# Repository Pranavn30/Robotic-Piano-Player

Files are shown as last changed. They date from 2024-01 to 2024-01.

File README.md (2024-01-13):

# Robotic-Piano-Player

Youtube Demonstration:

Robotic Piano Player (https://youtu.be/aeWdHynBX10)

The motivation of the project was to be able to emulate the functionality of a human playing the piano, mimicking the two "hands" of a human as well. We created this two hand structure by having two modules that move independently on two different belt drive linear actuators. The right hand plays three octaves and the left hand plays two octaves. Each hand is composed of 12 DC doorlock actuators which act as the fingers, and which are turned on and off by using I2C signals from GPIO expanders. These hands are then housed on custom 3D printed structures to hold all of the actuators in an exact and precise manner over the keys. Finally, the project has an LCD functionality which plays the music, as well as stops in and returns the hands to "home" position. The music files are downloaded and processed in a custom python script which decodes them, and is sent over USB to UART to the STM32. The data is then preprocessed within the firmware, optimizing the hand positions by grouping notes together, looking for movement opportunities, and overall making the system as efficient as possible. There is also speaker functionality (see below for further description).

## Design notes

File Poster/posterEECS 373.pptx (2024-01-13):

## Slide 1

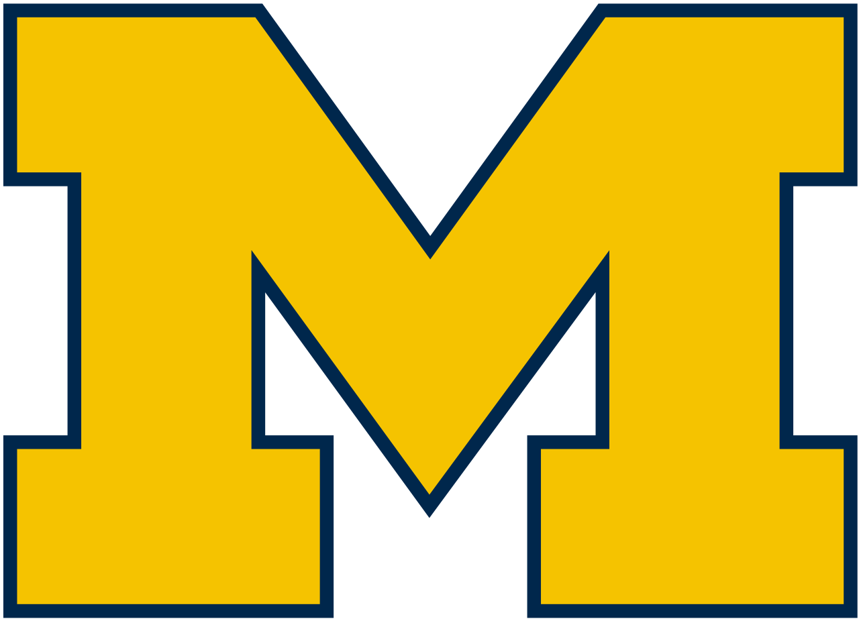
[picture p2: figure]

Robotic Piano Player

Pranav Narayanan, Daniel Moon, Zo-Vic Shong, Jesus Vidal Sanchez
{pranavn, danymoon, zovic, jesusvs}@umich.edu

EECS 373

MUSIC AND TECHNOLOGY COME TOGETHER TO EMULATE HUMAN PERFORMANCE SKILLS

- LCD screen allows the user to select which song will be played by the system.
- Uses a graphic library to display the interface
- Features a touchscreen so that the user can interact with the system
- Communicates with the STM through SPI

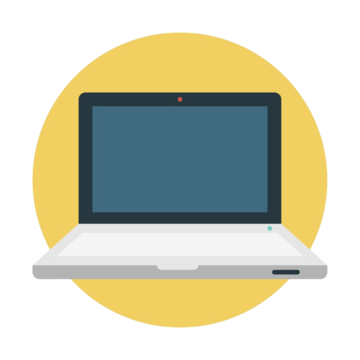
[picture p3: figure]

UART

It's Beginning To Look A Lot Like Christmas….

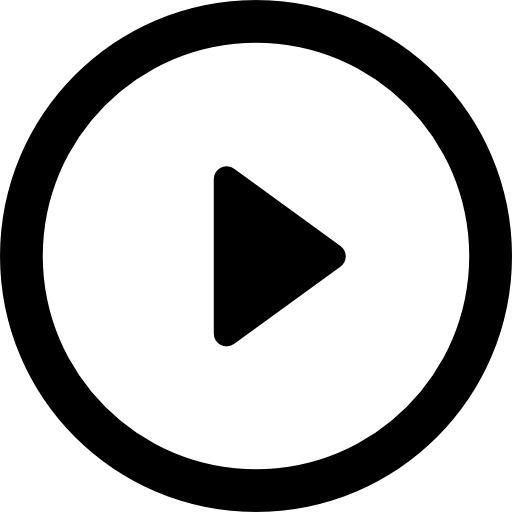
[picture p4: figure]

SPI

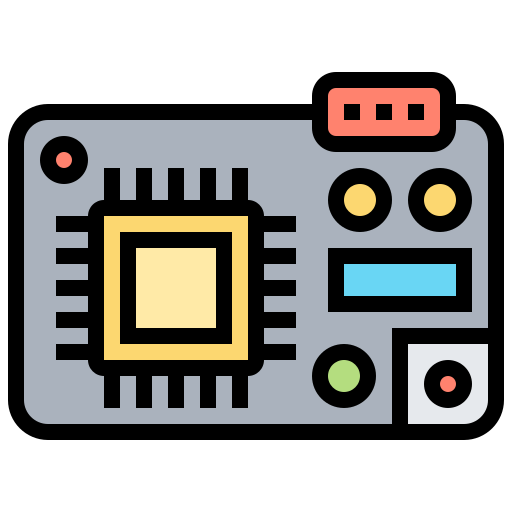
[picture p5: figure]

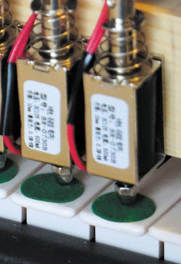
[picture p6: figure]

two hands
(3D printed structure)

Linear Actuators

Electromechanical
Belt Linear Actuator

- MIDI information is split into the respective two hands and proceeds through a complex algorithm to find the optimum times to move, and the ideal positions to play notes
- Entire system is controlled by timer interrupts which manage priorities and ordering of note playing

Arm Cortex M3

- The PC decodes information from locally stored MIDI files using Python

Python Script

- The Electromechanical Belt is used to move the hands horizontally in order to reach different note registers.
- We are using two belts, one for each hand so that they can move independently from each other. Each belt is moved by a Stepper Motor, connected to a Stepper Controller that makes them run at 2.8A of current.
- They are powered by a power source.

DAC

Speaker

- DC actuators are used to emulate human fingers:
- 12 dc actuators attached to each one of the two hands allow for triggering notes individually.
- The STM controls the voltage needed to trigger each actuator
- GPIO expanders needed to be used. They connect the actuators to the STM and use I2C protocol for communication.

- Due to the fact that some notes cannot be reached by our design, we implemented an external speaker.
- We will play notes out of range through the speaker instead of hitting keys
- It generates a sine wave to the corresponding frequency of the note intended to be played. The input to the speaker is the STM´s DAC.

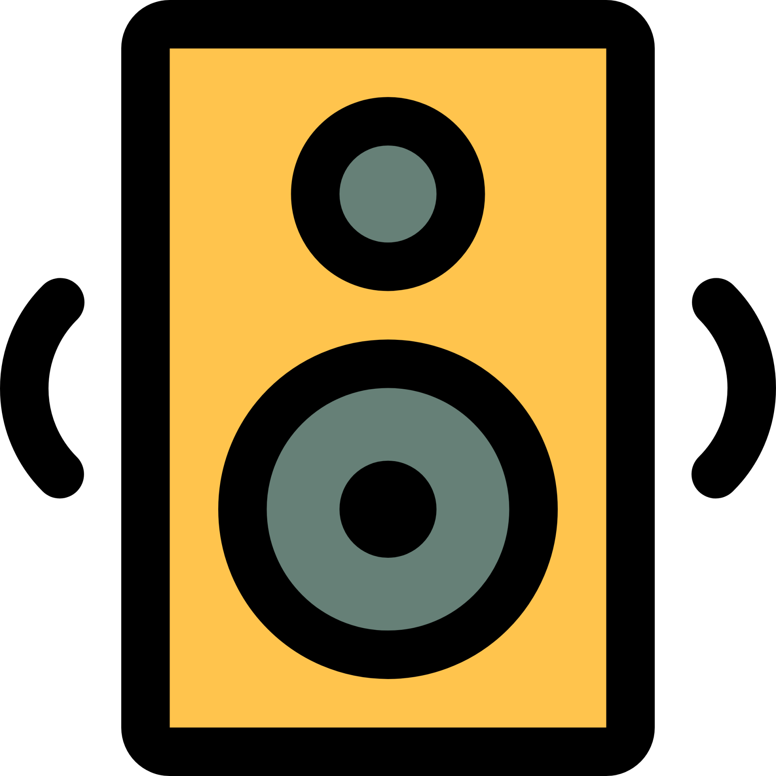
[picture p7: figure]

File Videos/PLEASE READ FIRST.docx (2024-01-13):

Hello Professors Sample and Smith, the best version of the video is linked in this document and in the README file within the digital archive folder, which includes a detailed description of the various parts. The video in here is the same but lacks the description

Link (https://youtu.be/aeWdHynBX10)

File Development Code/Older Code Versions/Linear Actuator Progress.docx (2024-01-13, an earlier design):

Linear Actuator Specifications:

2023.11.07

- Wire MCU, stepper motor controller, and stepper motor
- First attempts at coding, unsuccessful

2023.11.09

- Decide on belt drive for movement
- Successfully move stepper motor for first time

2023.11.11

- Use PWM for step control
- Get it moving faster
- Maximum step interval seems to depend on maximum voltage

2023.11.13

- Look up table (notes to distances)
- Equations for activation time to distance

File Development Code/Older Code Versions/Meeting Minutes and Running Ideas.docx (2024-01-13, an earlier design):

Interrupts get used if it is live actuation of the door lock actuators

FPGA lidar

Predictive algorithm using interrupts to determine next optimal position

Serial input in 2 note packets, preprocessed, determine optimal position of hand to enhance speed - possibly do this using fpga

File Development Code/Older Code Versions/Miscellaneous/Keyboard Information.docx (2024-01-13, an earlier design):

Full Keyboard Span - 33.5 Inches, 85 cm

White Key Thickness (also distance between white keys) - ⅞ Inches, 2.2 cm

Black Key Thickness - ⅜ Inches, 1 cm

Black Key Distance (#F, #G, #A) - 1 1/16 inches, 2.7 cm

Black Key Distance (#C, #D) - 1 ⅛ inches, 2.8 cm

Black Key Distance (#A, #C; #D, #F) - 1 ⅝ Inches, 4.2 cm

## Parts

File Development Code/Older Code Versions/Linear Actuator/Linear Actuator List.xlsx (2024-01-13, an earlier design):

Name | Length (inches) | Price | Link
Belt Drive Motorized Linear Stage Actuator 600MM | 23.622 | $209 | https://www.amazon.com/Motorized-Linear-Actuator-Motion-Position/dp/B07V1LRFPT
High Speed 700 MM 28 INCH Stroke Belt Drive | 28 | $195 | https://www.amazon.com/Stroke-Linear-Motion-Actuator-Position/dp/B07STNGVWS?sp_csd=d2lkZ2V0TmFtZT1zcF9hdGY
FUYU FSL40 Linear Guide Table | 19.685 | $195 | https://www.amazon.com/FUYU-Linear-Actuator-Motorized-Stepper/dp/B077Q8LVLW
RATTMMOTOR ZBX80 600mm | 23.622 | $215 | https://www.amazon.com/RATTMMOTOR-Actuator-Aluminum-Sliding-Ballscrew/dp/B09MYK424S
NEMA 23 Stepper Motor |  |  | STEPPERONLINE 3PCS Nema 23 CNC Stepper Motor 2.8A 1.26Nm/178.4oz.in 56mm Bipolar for Hobby CNC Kit - Amazon.com (https://www.amazon.com/STEPPERONLINE-Stepper-Motor-179oz-Bipolar/dp/B00QG1ZF48)

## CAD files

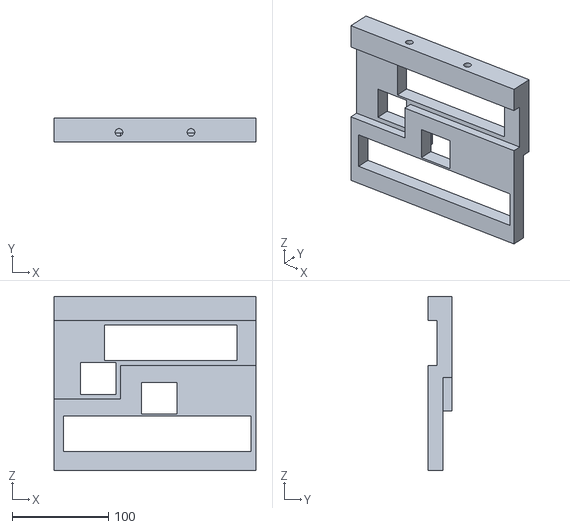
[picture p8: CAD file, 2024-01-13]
3D Print Files/DC Actuator Holder.STL
210.4 x 25.0 x 181.5

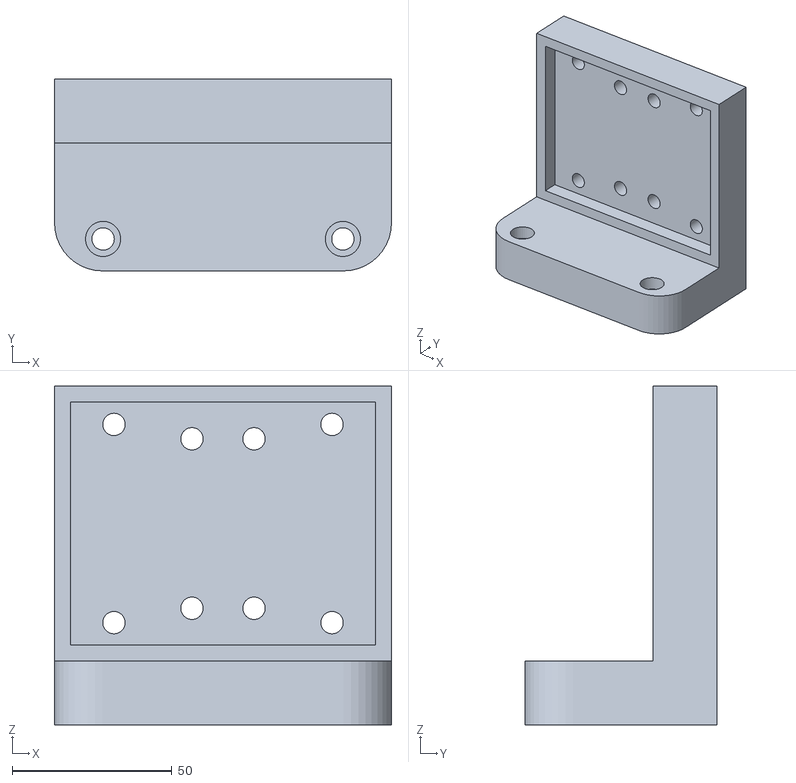
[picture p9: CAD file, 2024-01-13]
3D Print Files/DC Actuator Carriage Connector.STL
105.4 x 60.0 x 106.0

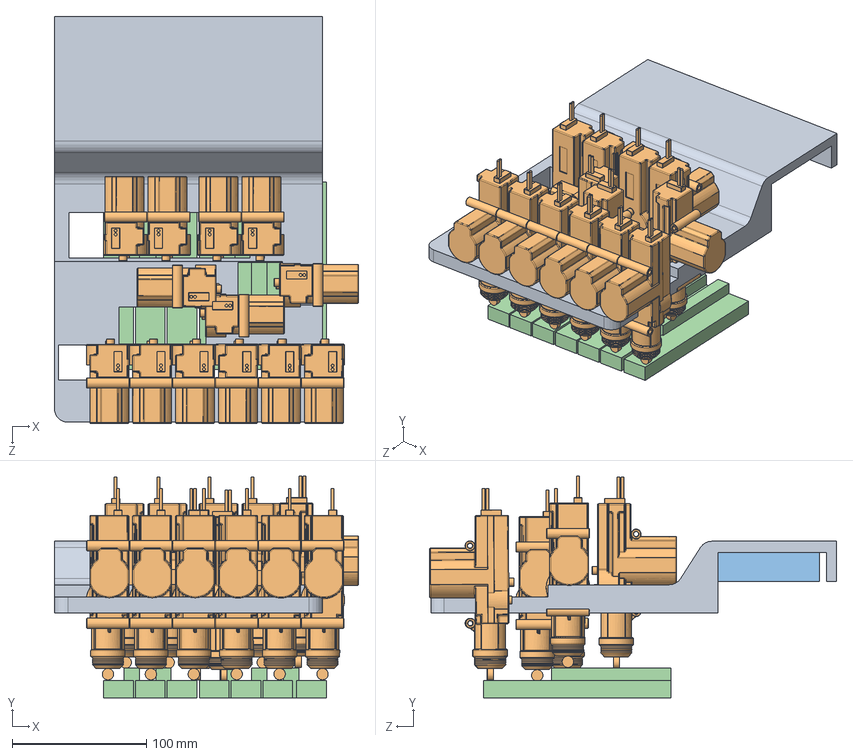
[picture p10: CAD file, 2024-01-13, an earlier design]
Development Code/Older Code Versions/CAD/373_Piano_Robot_Assembly_V2.SLDASM
226.8 x 165.2 x 303.5 mm
Piano_Keys
Rail_Carriage
DC_Actuator x 13
Linear_Actuator_Holder

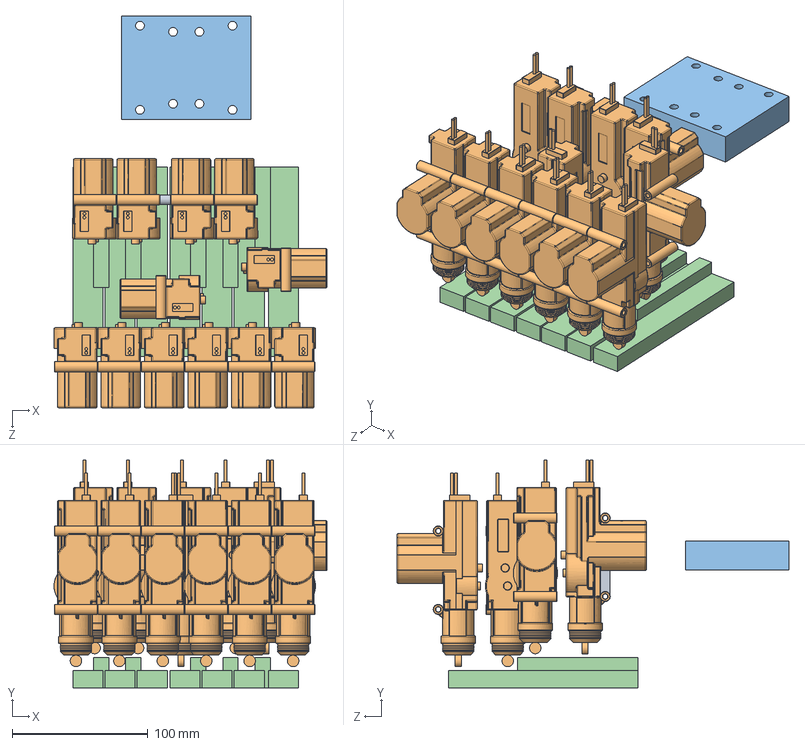
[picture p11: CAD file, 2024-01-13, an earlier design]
Development Code/Older Code Versions/CAD/373_Piano_Robot_Assembly.SLDASM
201.1 x 167.6 x 288.5 mm
Piano_Keys
Rail_Carriage_With Holes
DC_Actuator x 12
DC_Actuator_Black_Key_Spacer

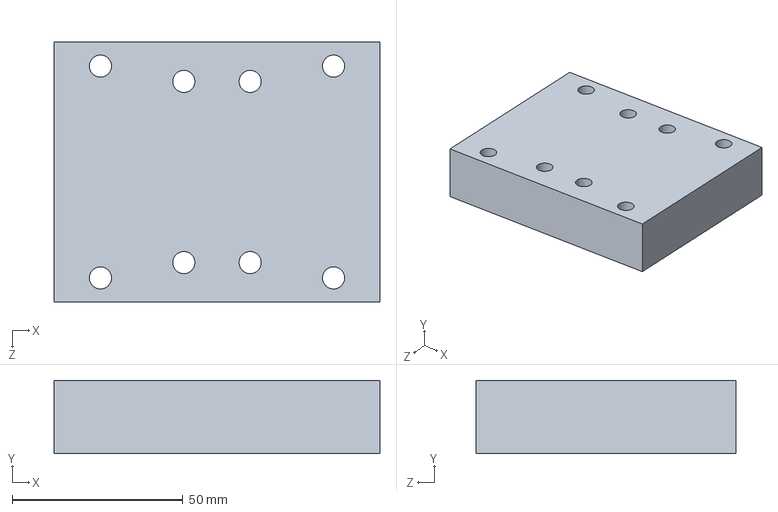
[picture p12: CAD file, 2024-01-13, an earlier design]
Development Code/Older Code Versions/CAD/Rail_Carriage_With Holes.SLDPRT
95.4 x 21.5 x 76.0 mm

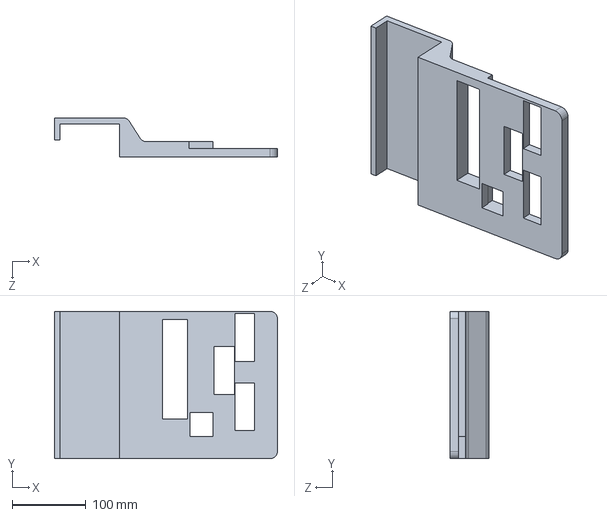
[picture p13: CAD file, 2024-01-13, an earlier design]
Development Code/Older Code Versions/CAD/Linear_Actuator_Holder.SLDPRT
302.5 x 200.0 x 53.5 mm

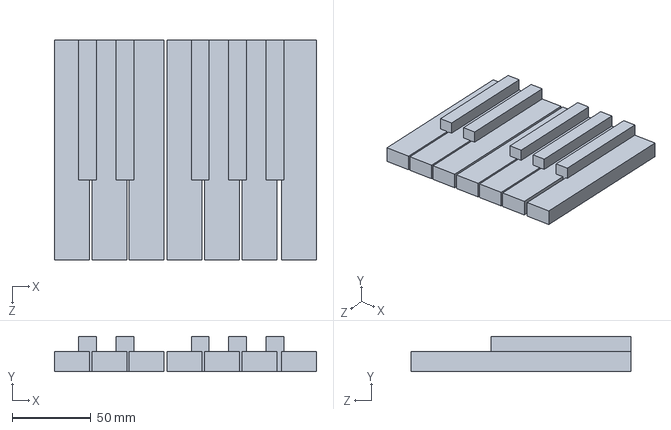
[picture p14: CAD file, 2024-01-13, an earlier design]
Development Code/Older Code Versions/CAD/Piano_Keys.SLDPRT
166.3 x 22.2 x 139.7 mm

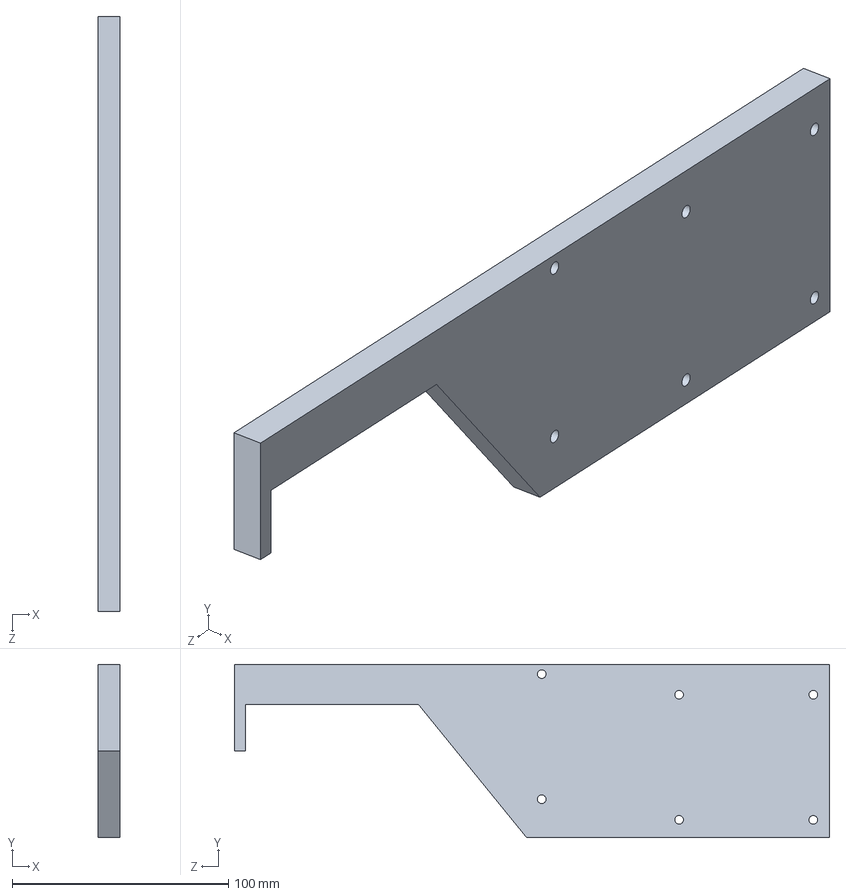
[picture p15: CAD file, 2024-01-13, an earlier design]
Development Code/Older Code Versions/CAD/Linear_Actuator_Support_Plate.SLDPRT
10.0 x 80.0 x 275.0 mm

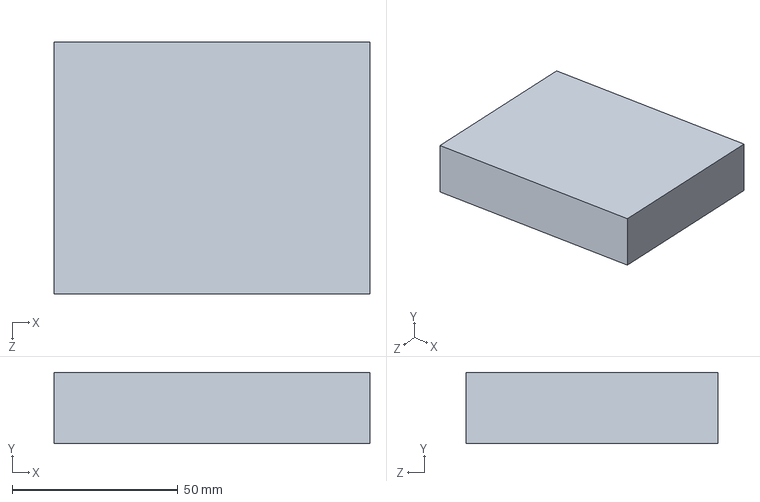
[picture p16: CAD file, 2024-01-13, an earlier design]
Development Code/Older Code Versions/CAD/Rail_Carriage.SLDPRT
95.4 x 21.5 x 76.0 mm

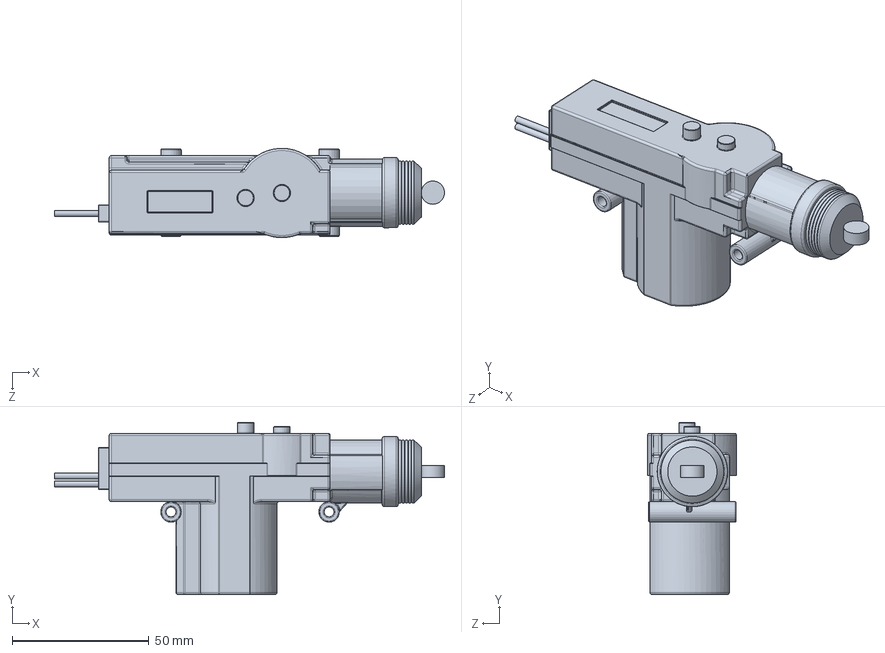
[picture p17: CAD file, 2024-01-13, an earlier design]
Development Code/Older Code Versions/CAD/DC_Actuator.SLDPRT
142.6 x 63.0 x 32.6 mm

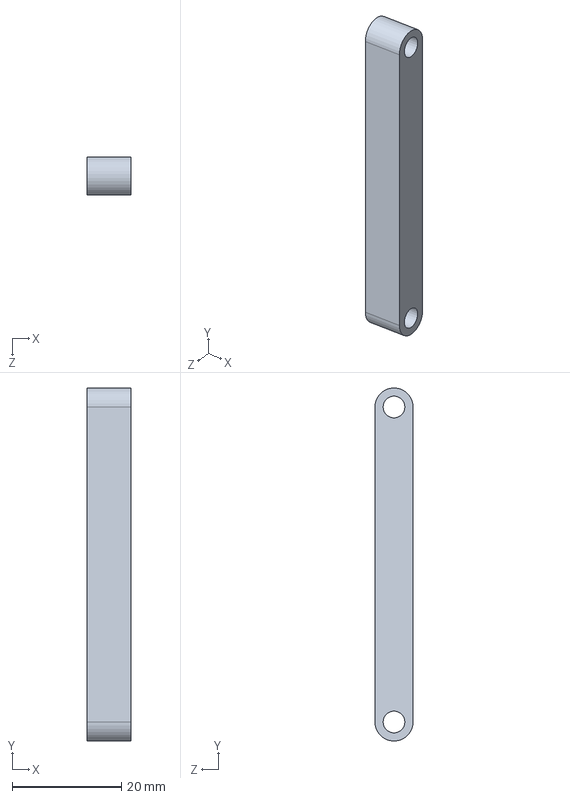
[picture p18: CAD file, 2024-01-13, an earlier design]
Development Code/Older Code Versions/CAD/DC_Actuator_Black_Key_Spacer.SLDPRT
8.00 x 64.8 x 7.00 mm

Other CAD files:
Development Code/Older Code Versions/CAD/DC_Actuator_Carriage_Connector_[PRINT].SLDPRT
Development Code/Older Code Versions/CAD/DC_Actuator_Holder_[PRINT].SLDPRT

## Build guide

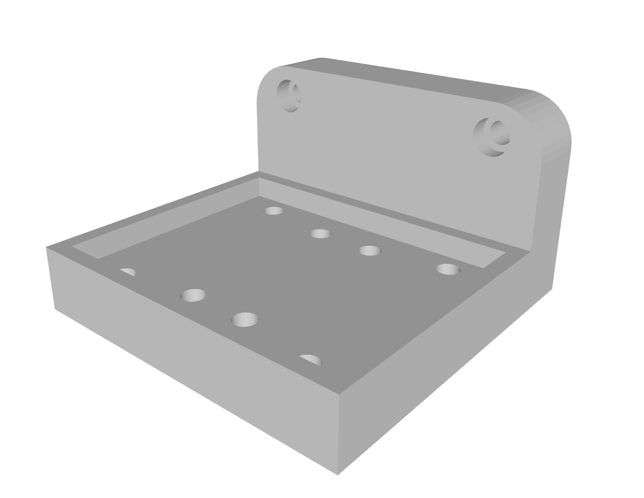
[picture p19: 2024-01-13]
3D Print Files/DC Actuator Carriage Connector.png

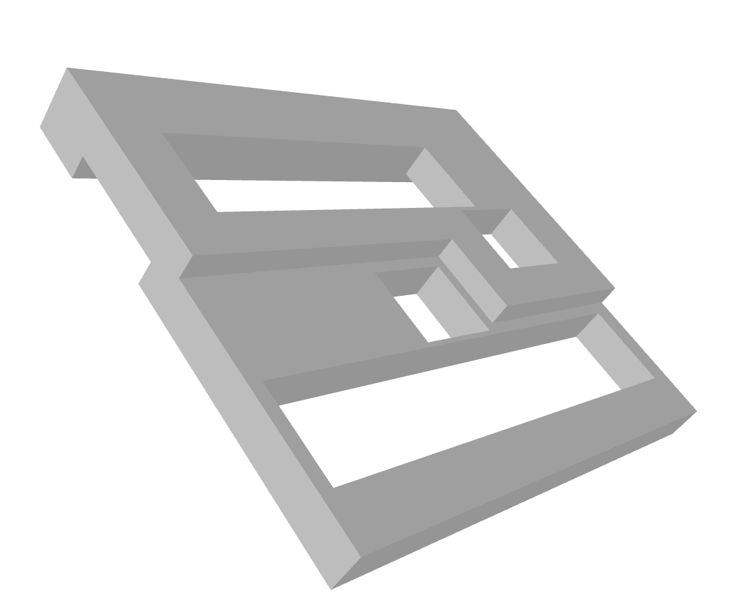
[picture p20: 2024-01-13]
3D Print Files/DC Actuator Holder.png

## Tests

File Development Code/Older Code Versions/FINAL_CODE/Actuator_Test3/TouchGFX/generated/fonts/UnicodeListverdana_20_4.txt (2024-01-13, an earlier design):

32
48
49
50
51
52
53
54
55
56
57
63
65
66
67
68
69
70
71
72
73
74
75
76
77
78
79
80
81
82
83
84
85
86
87
88
89
90
95
97
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

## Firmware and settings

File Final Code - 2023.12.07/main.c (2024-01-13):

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
/* Includes ------------------------------------------------------------------*/
#include "main.h"
#include "app_touchgfx.h"

/* USER CODE BEGIN Includes */
#include "math.h"
#include "stdlib.h"

/* USER CODE END Includes */

/* USER CODE BEGIN PD */
#define maxLetters 50

#define TIM7_PRSC 12
//look up table for sin wave generation
#define LUT_SIZE 100
uint16_t SIN_LUT[LUT_SIZE];
const double AMP_PCENT = 90.0; //amplitude of sine wave (0- 100)

/* USER CODE END PD */

CRC_HandleTypeDef hcrc;

DAC_HandleTypeDef hdac1;

I2C_HandleTypeDef hi2c1;
I2C_HandleTypeDef hi2c2;
I2C_HandleTypeDef hi2c3;
I2C_HandleTypeDef hi2c4;

SPI_HandleTypeDef hspi1;
SPI_HandleTypeDef hspi2;
DMA_HandleTypeDef hdma_spi1_tx;
DMA_HandleTypeDef hdma_spi2_tx;

TIM_HandleTypeDef htim2;
TIM_HandleTypeDef htim3;
TIM_HandleTypeDef htim4;
TIM_HandleTypeDef htim5;
TIM_HandleTypeDef htim7;

UART_HandleTypeDef huart2;
UART_HandleTypeDef huart3;

/* USER CODE BEGIN PV */
uint8_t RX_Buffer[5]; //"Interrupt!"
uint8_t TX_Buffer[] = "Hello World\r\n";
__IO uint8_t midi_titleBuffer[maxLetters] = "EECS 373 Robotic Piano Player";
__IO uint8_t rx_counter = 50;
__IO uint8_t midiTitleReady = 1;
/* USER CODE END PV */

void SystemClock_Config(void);
static void MX_GPIO_Init(void);
static void MX_DMA_Init(void);
static void MX_USART2_UART_Init(void);
static void MX_USART3_UART_Init(void);
static void MX_TIM5_Init(void);
static void MX_TIM2_Init(void);
static void MX_TIM3_Init(void);
static void MX_TIM4_Init(void);
static void MX_I2C1_Init(void);
static void MX_I2C2_Init(void);
static void MX_I2C3_Init(void);
static void MX_I2C4_Init(void);
static void MX_SPI1_Init(void);
static void MX_SPI2_Init(void);
static void MX_CRC_Init(void);
static void MX_DAC1_Init(void);
static void MX_TIM7_Init(void);
/* USER CODE BEGIN 0 */
void fill_LUT(void)
{
	//creates a sine wave look up table centered at VREF/2
	double HALF_AMP = (AMP_PCENT/ 100.0) * 2047.0;//calculates a half amplitude given the desired volume
	uint16_t i = 0;
	for(; i < LUT_SIZE; ++i)
	{
		SIN_LUT[i] = (uint16_t) ( (sin( ( (double) i) * 360.0 / ((double) LUT_SIZE)  * 3.14159265/180.0) * HALF_AMP) + 2048.0);
	}
}

//sets compare value (period) for tim2
void setComp(uint32_t newComp)
{
	HAL_TIM_Base_Stop(&htim7);
	htim7.Instance = TIM7;
	htim7.Init.Prescaler = TIM7_PRSC;
	htim7.Init.CounterMode = TIM_COUNTERMODE_UP;
	htim7.Init.Period = newComp;
	htim7.Init.ClockDivision = TIM_CLOCKDIVISION_DIV1;
	htim7.Init.AutoReloadPreload = TIM_AUTORELOAD_PRELOAD_DISABLE;
	if (HAL_TIM_Base_Init(&htim7) != HAL_OK)
	{
		Error_Handler();
	}

	HAL_TIM_Base_Start(&htim7);
}

//frequency = tim2_clk/tim2_prsclr/LUT_SIZE/tim2_prd
//desired tim2_prd = tm2_clk/tim2_prsclr/LUT_SIZE/frequency
//tim2_clk = 120 MHz, tim2_prsclr = 85, LUT_SIZE = 100
void changeNote(float frequency)
{
	setComp((uint32_t) (120000000.0f/TIM7_PRSC/((float)LUT_SIZE)/frequency) );
}

void speakNote(int noteNum)
{
	HAL_DAC_Start(&hdac1, DAC_CHANNEL_1);
	float arg = (float)((noteNum + 3 + 11 - 69)/12.0);
	float frequency = pow(2,arg)*440;
	//printf("frecuencia:  %f \n\r", (float)frequency);
	changeNote(frequency);
}

void stopSpeaker()
{
	HAL_DAC_Stop(&hdac1, DAC_CHANNEL_1);
}

//used to iterate through the LUT
void TIM7_ISR()
{
	static uint32_t index = 0;
	HAL_DAC_SetValue(&hdac1, DAC_CHANNEL_1, DAC_ALIGN_12B_R, SIN_LUT[index]);
	++index;
	if(index > LUT_SIZE) index = 0;
}


#define Motor1A GPIO_PIN_0
#define Motor1B GPIO_PIN_1
#define Motor2A GPIO_PIN_2
#define Motor2B GPIO_PIN_3

#define Motor3A GPIO_PIN_11
#define Motor3B GPIO_PIN_5
#define Motor4A GPIO_PIN_4
#define Motor4B GPIO_PIN_10


void forward(GPIO_TypeDef* GPIOX, uint16_t MotorA, uint16_t MotorB)
{
    HAL_GPIO_WritePin(GPIOX, MotorA, GPIO_PIN_RESET);
    HAL_GPIO_WritePin(GPIOX, MotorB, GPIO_PIN_SET);
}

void backward(GPIO_TypeDef* GPIOX, uint16_t MotorA, uint16_t MotorB)
{
    HAL_GPIO_WritePin(GPIOX, MotorA, GPIO_PIN_SET);
    HAL_GPIO_WritePin(GPIOX, MotorB, GPIO_PIN_RESET);
}

void stop(GPIO_TypeDef* GPIOX, uint16_t MotorA, uint16_t MotorB)
{
    HAL_GPIO_WritePin(GPIOX, MotorA, GPIO_PIN_RESET);
    HAL_GPIO_WritePin(GPIOX, MotorB, GPIO_PIN_RESET);
}

#define MAX_GROUP_SIZE 3 // Maximum number of notes in a group
#define MAX_NOTE_DISTANCE 3 // Maximum distance between notes in a group

#define sizeLimit 2000
#define noteColNum 5
#define lowestNote 36
#define highestNote 96
#define defaultRight 60
#define defaultLeft 43
#define DCDelay 250
#define INT_MAX 2147483647

int actuatorPosL[sizeLimit][2];
int actuatorPosL_len = 0;
int actuatorPosR[sizeLimit][2];
int actuatorPosR_len = 0;

int song_length = 0;
int read_notes = 0;

int reading_title = 0;
char title_data[50];
int title_index = 0;

int actuatorL = 0;
int actuatorR = 0;

int DCLeftStart = 0;
int DCLeftStop = 0;
int DCRightStart = 0;
int DCRightStop = 0;

int note_dataL[sizeLimit][noteColNum];
int note_dataL_len = 0;
int note_dataR[sizeLimit][noteColNum];
int note_dataR_len = 0;

int note_dataR_stop[sizeLimit][2];
int note_dataL_stop[sizeLimit][2];

double current_pos_left = 0;
double current_pos_right = 0;

int readyToPlay = 0;

int formGroups(int noteArr[][noteColNum], int len);
int groupRange(int noteArr[][noteColNum], int len, int group1, int group2);
void groupMerge(int noteArr[][noteColNum], int len, int group1, int group2);
void groupContinuity(int noteArr[][noteColNum], int len);
void movementOps(int noteArr[][noteColNum], int len);
int assignActuatorPos(int actuatorPos[][2], int noteArr[][noteColNum], int note_len, int hand);
void splitStartStop(int noteArr[][noteColNum], int note_len, int noteArrStop[][2]);
void sortStop(int noteArr[][2], int note_len);
void assignDCAct(int actuatorPos[][2], int actuator_len, int noteArr[][noteColNum], int note_len);
void moveActuatorLeft(int note_num);
void moveActuatorRight(int note_num);
int nearestMinWhite(int noteNum);
int nearestMaxWhite(int noteNum);
int isBlackKey(int noteNum);
int setNextLinActuatorTime(int current_time);
void actuatorMoveDistLoop(double dist, int dir, int hand);
void GPIO_Activation_Right(int note);
void GPIO_Activation_Left(int note);
void GPIO_Deactivation_Right(int note);
void GPIO_Deactivation_Left(int note);
int setDCStart(int current_time);
int setDCStop(int current_time);
void setNextAction(int current_time);

int formGroups(int noteArr[][noteColNum], int len){
	movementOps(noteArr, len);
	int num_groups = noteArr[len - 1][3];
	for(int i = 0; i < num_groups; i++){
		if(groupRange(noteArr, len, i, i + 1) <= 11){
			groupMerge(noteArr, len, i, i + 1);
			num_groups--;
			groupContinuity(noteArr, len);
			i--;
		}
	}
	return 0;
}

// Given two group numbers, return the collective range
int groupRange(int noteArr[][noteColNum], int len, int group1, int group2){
	int minNote = 100;
	int maxNote = 0;
	for(int i = 0; i < len; i++){
		if(noteArr[i][3] == group1 || noteArr[i][3] == group2){
			if(noteArr[i][4] == 0){
				int min = nearestMinWhite(noteArr[i][0]);
				int max = nearestMaxWhite(noteArr[i][0]);
				if(min < minNote){
					minNote = min;
				}
				if(max > maxNote){
					maxNote = max;
				}
			}
		}
	}
	return maxNote - minNote;
}

// Identify the nearest white note under the argument note number
int nearestMinWhite(int noteNum){
	if(isBlackKey(noteNum)){
		return noteNum - 1;
	}
	return noteNum;
}

// Identify the nearest white note above the argument note number
int nearestMaxWhite(int noteNum){
	if(isBlackKey(noteNum)){
			return noteNum + 1;
		}
		return noteNum;
}


// Identify if a note is a black key
int isBlackKey(int noteNum){
	int isBlack = noteNum % 12;
	if(isBlack == 1 || isBlack == 3 || isBlack == 6 || isBlack == 8 || isBlack == 10){
		return 1;
	}
	return 0;
}
// Given two consecutive groups, combine them into one group using the lower group number; assumes group1 < group2
void groupMerge(int noteArr[][noteColNum], int len, int group1, int group2){
	for(int i = 0; i < len; i++){
		if(noteArr[i][3] == group2){
			noteArr[i][3] = group1;
		}
	}
}

// Reassign group numbers so they are sequential in value
void groupContinuity(int noteArr[][noteColNum], int len){
	int prevGroupNum = 0;
	int replaceGroup = 0;
	int newGroupNum = 0;
	int diff = 0;
	for(int i = 0; i < len; i++){
		diff = noteArr[i][3] - prevGroupNum;
		if(diff > 1 || diff < 0){
			replaceGroup = noteArr[i][3];
			newGroupNum = prevGroupNum + 1;
			while(noteArr[i][3] == replaceGroup && (i < len)){
				noteArr[i][3] = newGroupNum;
				i++;
			}
			i--;
		}
		prevGroupNum = noteArr[i][3];
	}
}

// Search for all movement opportunities and use them as divisions between groups
void movementOps(int noteArr[][noteColNum], int len){
	int current_group = 0;
	int time_max = noteArr[0][2];
	noteArr[0][3] = 0;
	for(int i = 1; i < len; i++){
		if(noteArr[i][1] > time_max){
			current_group++;
			noteArr[i][3] = current_group;
			time_max = noteArr[i][2];
		}
		else if(noteArr[i][2] > time_max){
			time_max = noteArr[i][2];
			noteArr[i][3] = current_group;
		}
		else{
			noteArr[i][3] = current_group;
		}
	}
}

// Assign actuator positions using a note data array
int assignActuatorPos(int actuatorPos[][2], int noteArr[][noteColNum], int note_len, int hand){
	if(note_len < 1){
		return 0;
	}
	int current_group = 0;
	int group_min_note = nearestMinWhite(noteArr[0][0]);
	int group_min_time = noteArr[0][1];
	for(int i = 0; i < note_len; i++){
		if(noteArr[i][3] != current_group){
			if(group_min_note > highestNote || group_min_note < lowestNote || (hand && group_min_note > defaultLeft) || (!hand && group_min_note < defaultRight)){
				if(hand){
					actuatorPos[current_group][0] = defaultLeft;
				}
				else{
					actuatorPos[current_group][0] = defaultRight;
				}
			}
			else{
				actuatorPos[current_group][0] = group_min_note;
			}
			actuatorPos[current_group][1] = group_min_time;
			if(!noteArr[i][4]){
				group_min_note = nearestMinWhite(noteArr[i][0]);
			}
			else{
				group_min_note = 100;
			}
			group_min_time = noteArr[i][1];
			current_group = noteArr[i][3];
		}
		else if(noteArr[i][0] < group_min_note && !noteArr[i][4]){
				group_min_note = nearestMinWhite(noteArr[i][0]);
		}
	}
	if(group_min_note > highestNote || group_min_note < lowestNote || (hand && group_min_note > defaultLeft) || (!hand && group_min_note < defaultRight)){
		if(hand){
			actuatorPos[current_group][0] = defaultLeft;
		}
		else{
			actuatorPos[current_group][0] = defaultRight;
		}
	}
	else{
		actuatorPos[current_group][0] = group_min_note;
	}
	actuatorPos[current_group][1] = group_min_time;

	return current_group + 1;
}

// Split start and stop times for notes
void splitStartStop(int noteArr[][noteColNum], int note_len, int noteArrStop[][2]){
	for(int i = 0; i < note_len; i++){
		noteArrStop[i][0] = noteArr[i][0];
		noteArrStop[i][1] = noteArr[i][2];
	}
}

// Sort stop array
void sortStop(int noteArr[][2], int note_len){
	int key_note, key_time, j;
	for(int i = 1; i < note_len; i++){
		key_note = noteArr[i][0];
		key_time = noteArr[i][1];
		j = i - 1;

		while(j >= 0 && noteArr[j][1] > key_time){
			noteArr[j + 1][0] = noteArr[j][0];
			noteArr[j + 1][1] = noteArr[j][1];
			j--;
		}
		noteArr[j + 1][0] = key_note;
		noteArr[j + 1][1] = key_time;
	}
}

// 12 indicates note should be played on speaker
int DCLookup[][12] = {
		{0, 1, 2, 3, 4, 5, 6, 7, 8, 9, 10, 11},
		{0, 0, 0, 0, 0, 0, 0, 0, 0, 0, 0, 0},
		{11, 12, 0, 1, 2, 4, 12, 5, 6, 7, 8, 9},
		{0, 0, 0, 0, 0, 0, 0, 0, 0, 0, 0, 0},
		{9, 10, 11, 12, 0, 2, 3, 4, 12, 5, 6, 7},
		{7, 8, 9, 10, 11, 0, 1, 2, 3, 4, 12, 5},
		{0, 0, 0, 0, 0, 0, 0, 0, 0, 0, 0, 0},
		{5, 6, 7, 8, 9, 11, 12, 0, 1, 2, 3, 4},
		{0, 0, 0, 0, 0, 0, 0, 0, 0, 0, 0, 0},
		{4, 12, 5, 6, 7, 9, 10, 11, 12, 0, 1, 2},
		{0, 0, 0, 0, 0, 0, 0, 0, 0, 0, 0, 0},
		{2, 3, 4, 12, 5, 7, 8, 9, 10, 11, 12, 0},
};

// Assign DC actuator activations
void assignDCAct(int actuatorPos[][2], int actuator_len, int noteArr[][noteColNum], int note_len){
	int DCNum = 0;
	for(int i = 0; i < note_len; i++){
		if(!noteArr[i][4]){
			DCNum = DCLookup[actuatorPos[(noteArr[i][3])][0] % 12][noteArr[i][0] % 12];
			if(DCNum < 12){
				noteArr[i][0] = DCNum;
			}
		}

	}
}

int nextMove = 0;

// Sets TIM2 ARR so that it triggers for the next linear actuator movement
// Returns 0 if there is no next linear actuator movement
int setNextLinActuatorTime(int current_time){
	if(actuatorL >= actuatorPosL_len){
		if(actuatorR >= actuatorPosR_len){
			//HAL_TIM_Base_Stop_IT(&htim2);
			//return 0;
			return INT_MAX;
		}
		else{
			//TIM2->ARR = actuatorPosR[actuatorR][1] - current_time - 1;
			return actuatorPosR[actuatorR][1] - current_time;
		}
	}
	else if(actuatorR >= actuatorPosR_len){
		if(actuatorL >= actuatorPosL_len){
			//HAL_TIM_Base_Stop_IT(&htim2);
			//return 0;
		}
		else{
			//TIM2->ARR = actuatorPosL[actuatorL][1] - current_time - 1;
			return actuatorPosL[actuatorL][1] - current_time;
		}
	}
	else if(actuatorPosL[actuatorL][1] < actuatorPosR[actuatorR][1]){
		//TIM2->ARR = actuatorPosL[actuatorL][1] - current_time - 1;
		return actuatorPosL[actuatorL][1] - current_time;
	}
	else{
		//TIM2->ARR = actuatorPosR[actuatorR][1] - current_time - 1;
		return actuatorPosR[actuatorR][1] - current_time;
	}

	return 1;
}


// Sets TIM3 ARR so that it triggers for the next DC actuator push
// Returns 0 if there is no next DC actuator push
int setDCStart(int current_time){
	if(DCLeftStart >= note_dataL_len){
		if(DCRightStart >= note_dataR_len){
			HAL_TIM_Base_Stop_IT(&htim3);
			//return 0;
			return INT_MAX;
		}
		else{
			//TIM3->ARR = note_dataR[DCRightStart][1] - current_time - 1;
			return note_dataR[DCRightStart][1] - current_time;
		}
	}
	else if(DCRightStart >= note_dataR_len){
		if(DCLeftStart >= note_dataL_len){
			HAL_TIM_Base_Stop_IT(&htim3);
			//return 0;
			return INT_MAX;
		}
		else{
			//TIM3->ARR = note_dataL[DCLeftStart][1] - current_time - 1;
			return note_dataL[DCLeftStart][1] - current_time;
		}
	}
	else if(note_dataL[DCLeftStart][1] < note_dataR[DCRightStart][1]){
		//TIM3->ARR = note_dataL[DCLeftStart][1] - current_time - 1;
		return note_dataL[DCLeftStart][1] - current_time;
	}
	else{
		//TIM3->ARR = note_dataR[DCRightStart][1] - current_time - 1;
		return note_dataR[DCRightStart][1] - current_time;
	}
	return 1;
}

// Sets TIM4 ARR so that it triggers for the next DC actuator pull
// Returns 0 if there is no next DC actuator pull
int setDCStop(int current_time){
	if(DCLeftStop >= note_dataL_len){
		if(DCRightStop >= note_dataR_len){
			HAL_TIM_Base_Stop_IT(&htim4);
			// return 0;
			return INT_MAX;
		}
		else{
			//TIM4->ARR = note_dataR_stop[DCRightStop][1] - current_time - 1;
			return note_dataR_stop[DCRightStop][1] - current_time ;
		}
	}
	else if(DCRightStop >= note_dataR_len){
		if(DCLeftStop >= note_dataL_len){
			HAL_TIM_Base_Stop_IT(&htim4);
			//return 0;
			return INT_MAX;
		}
		else{
			//TIM4->ARR = note_dataL_stop[DCLeftStop][1] - current_time - 1;
			return note_dataL_stop[DCLeftStop][1] - current_time;
		}
	}
	else if(note_dataL_stop[DCLeftStop][1] < note_dataR_stop[DCRightStop][1]){
		//TIM4->ARR = note_dataL_stop[DCLeftStop][1] - current_time - 1;
		return note_dataL_stop[DCLeftStop][1] - current_time;
	}
	else{
		//TIM4->ARR = note_dataR_stop[DCRightStop][1] - current_time - 1;
		return note_dataR_stop[DCRightStop][1] - current_time;
	}
	return 1;
}
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
int main(void)
{
  /* MCU Configuration--------------------------------------------------------*/

  /* Reset of all peripherals, Initializes the Flash interface and the Systick. */
  HAL_Init();

  /* Configure the system clock */
  SystemClock_Config();

  /* Initialize all configured peripherals */
  MX_GPIO_Init();
  MX_DMA_Init();
  MX_USART2_UART_Init();
  MX_USART3_UART_Init();
  MX_TIM5_Init();
  MX_TIM2_Init();
  MX_TIM3_Init();
  MX_TIM4_Init();
  MX_I2C1_Init();
  MX_I2C2_Init();
  MX_I2C3_Init();
  MX_I2C4_Init();
  MX_SPI1_Init();
  MX_SPI2_Init();
  MX_CRC_Init();
  MX_DAC1_Init();
  MX_TIM7_Init();
  MX_TouchGFX_Init();
  /* USER CODE BEGIN 2 */
	HAL_GPIO_TogglePin(GPIOB, GPIO_PIN_7);
	HAL_Delay(3000);
	HAL_GPIO_TogglePin(GPIOB, GPIO_PIN_7);

	fill_LUT();

	HAL_DAC_SetValue(&hdac1, DAC_CHANNEL_1, DAC_ALIGN_12B_R, 0x0);
	HAL_DAC_Start(&hdac1, DAC_CHANNEL_1);
	stopSpeaker();
	HAL_TIM_Base_Start_IT(&htim7);

  Displ_Init(Displ_Orientat_270);		// initialize the display and set the initial display orientation (here is orientaton: 0°) - THIS FUNCTION MUST PRECEED ANY OTHER DISPLAY FUNCTION CALL.
   touchgfxSignalVSync();		// asks TouchGFX to start initial display drawing
   Displ_BackLight('I');  			// initialize backlight and turn it on at init level

  //********************************************************
  // Might need to move this to where ever we start the song
  //********************************************************

  HAL_TIM_PWM_Start(&htim5, TIM_CHANNEL_4);
  TIM5->CCR4 = 25;

  HAL_UART_Receive_IT(&huart3, RX_Buffer, sizeof(RX_Buffer));
  HAL_UART_Transmit_IT(&huart3, TX_Buffer, sizeof(TX_Buffer));
  HAL_GPIO_WritePin(GPIOF, GPIO_PIN_8, 1);

  /*uint8_t P01_OFF[1] = {0x02};
  uint8_t P01_STOP[1] = {0x00};*/
  /*HAL_I2C_Master_Transmit(&hi2c1, (0x20<<1), &P01_OFF[0], 1, 1000);
  HAL_Delay(150);
  HAL_I2C_Master_Transmit(&hi2c1, (0x20<<1), &P01_STOP[0], 1, 1000);*/

  /*HAL_GPIO_WritePin(GPIOF, GPIO_PIN_8, 1);
  HAL_GPIO_WritePin(GPIOF, GPIO_PIN_7, 1);
  //moveActuatorDistRight(0.93, 1);
  HAL_I2C_Master_Transmit(&hi2c1, (0x20<<1), &data_write3[0], 1, 1000);
  HAL_Delay(200);
  HAL_I2C_Master_Transmit(&hi2c1, (0x20<<1), &data_write2[0], 1, 1000);
  HAL_Delay(200);
  actuatorMoveDistLoop(0.93 * 7, 1);
  HAL_Delay(100);
  ON1_PCF8574();
  actuatorMoveDistLoop(0.93 * 7, 1);
  HAL_Delay(100);
  ON1_PCF8574();
  actuatorMoveDistLoop(0.93 * 7, 0);
  HAL_Delay(100);
  ON1_PCF8574();
  actuatorMoveDistLoop(0.93 * 7, 0);
  HAL_Delay(100);
  ON1_PCF8574();
  HAL_I2C_Master_Transmit(&hi2c1, (0x20<<1), &data_write3[0], 1, 1000);
   HAL_Delay(200);
   HAL_I2C_Master_Transmit(&hi2c1, (0x20<<1), &data_write2[0], 1, 1000);
   HAL_Delay(200);*/

  /*moveActuatorDist(16.25, 1);
  HAL_Delay(100);
  forward(GPIOA, Motor1A, Motor1B);
  forward(GPIOA, Motor2A, Motor2B);
  HAL_Delay(150);
  backward(GPIOA, Motor1A, Motor1B);
  backward(GPIOA, Motor2A, Motor2B);
  HAL_Delay(150);
  forward(GPIOA, Motor1A, Motor1B);
  forward(GPIOA, Motor2A, Motor2B);
  HAL_Delay(150);
  backward(GPIOA, Motor1A, Motor1B);
  backward(GPIOA, Motor2A, Motor2B);
  HAL_Delay(100);

  moveActuatorDist(16.25, 0);
  HAL_Delay(100);
  forward(GPIOA, Motor1A, Motor1B);
  forward(GPIOA, Motor2A, Motor2B);
  HAL_Delay(100);
  backward(GPIOA, Motor1A, Motor1B);
  backward(GPIOA, Motor2A, Motor2B);

  stop(GPIOA, Motor1A, Motor1B);
  stop(GPIOA, Motor2A, Motor2B);*/
  /*HAL_GPIO_WritePin(GPIOF, GPIO_PIN_8, 1);
  HAL_GPIO_WritePin(GPIOF, GPIO_PIN_7, 1);
  HAL_GPIO_WritePin(GPIOF, GPIO_PIN_8, 0);
  for(int i = 0; i < 200; i++){
  	HAL_GPIO_WritePin(GPIOG, GPIO_PIN_0, 1);
  	HAL_Delay(1);
  	HAL_GPIO_WritePin(GPIOG, GPIO_PIN_0, 0);
  	HAL_Delay(199);
  }
  HAL_GPIO_WritePin(GPIOF, GPIO_PIN_8, 1);*/

  /*HAL_GPIO_WritePin(GPIOF, GPIO_PIN_8, 1);
  HAL_GPIO_WritePin(GPIOF, GPIO_PIN_7, 1);
  HAL_GPIO_WritePin(GPIOF, GPIO_PIN_8, 0);
  HAL_Delay(1000);
  HAL_GPIO_WritePin(GPIOF, GPIO_PIN_8, 1);*/
  /* USER CODE END 2 */

  /* Infinite loop */
  /* USER CODE BEGIN WHILE */
   int pressed = 0;
   int start = 0;
   int playingSong = 0;
   int prevTouch = 0;
   int currentTouch = 0;


  	  GPIO_Activation_Right(11);
  	  GPIO_Deactivation_Right(11);

  	  GPIO_Activation_Right(10);
  	  GPIO_Deactivation_Right(10);

  	  GPIO_Activation_Right(9);
  	  GPIO_Deactivation_Right(9);

  	  GPIO_Activation_Right(8);
  	  GPIO_Deactivation_Right(8);

  	  GPIO_Activation_Right(7);
  	  GPIO_Deactivation_Right(7);

  	  GPIO_Activation_Right(6);
  	  GPIO_Deactivation_Right(6);

  	  GPIO_Activation_Right(5);
  	  GPIO_Deactivation_Right(5);

  	  GPIO_Activation_Right(4);
  	  GPIO_Deactivation_Right(4);

  	  GPIO_Activation_Right(3);
  	  GPIO_Deactivation_Right(3);

  	  GPIO_Activation_Right(2);
  	  GPIO_Deactivation_Right(2);

  	  GPIO_Activation_Right(1);
  	  GPIO_Deactivation_Right(1);

  	  GPIO_Activation_Right(0);
  	  GPIO_Deactivation_Right(0);


  	  GPIO_Activation_Right(59);
  	  GPIO_Deactivation_Right(59);

  	  GPIO_Activation_Right(58);
  	  GPIO_Deactivation_Right(58);

  	  GPIO_Activation_Right(57);
  	  GPIO_Deactivation_Right(57);

  	  GPIO_Activation_Right(56);
  	  GPIO_Deactivation_Right(56);

  	  GPIO_Activation_Right(55);
  	  GPIO_Deactivation_Right(55);

  	GPIO_Activation_Left(11);
  	GPIO_Deactivation_Left(11);

  	GPIO_Activation_Left(10);
  	GPIO_Deactivation_Left(10);

  	GPIO_Activation_Left(9);
  	GPIO_Deactivation_Left(9);

  	GPIO_Activation_Left(8);
  	GPIO_Deactivation_Left(8);

  	GPIO_Activation_Left(7);
  	GPIO_Deactivation_Left(7);

  	GPIO_Activation_Left(6);
  	GPIO_Deactivation_Left(6);

  	GPIO_Activation_Left(5);
  	GPIO_Deactivation_Left(5);

  	GPIO_Activation_Left(4);
  	GPIO_Deactivation_Left(4);

  	GPIO_Activation_Left(3);
  	GPIO_Deactivation_Left(3);

  	GPIO_Activation_Left(2);
  	GPIO_Deactivation_Left(2);

  	GPIO_Activation_Left(1);
  	GPIO_Deactivation_Left(1);

  	GPIO_Activation_Left(0);
  	GPIO_Deactivation_Left(0);
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

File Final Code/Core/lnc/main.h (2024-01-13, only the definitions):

#define TOUCH_MISO_Pin GPIO_PIN_2
#define TOUCH_MISO_GPIO_Port GPIOC
#define TOUCH_MOSI_Pin GPIO_PIN_3
#define TOUCH_MOSI_GPIO_Port GPIOC
#define DISPL_SCK_Pin GPIO_PIN_5
#define DISPL_SCK_GPIO_Port GPIOA
#define DISPL_MISO_Pin GPIO_PIN_6
#define DISPL_MISO_GPIO_Port GPIOA
#define DISPL_MOSI_Pin GPIO_PIN_7
#define DISPL_MOSI_GPIO_Port GPIOA
#define DISPL_RST_Pin GPIO_PIN_12
#define DISPL_RST_GPIO_Port GPIOF
#define DISPL_CS_Pin GPIO_PIN_13
#define DISPL_CS_GPIO_Port GPIOF
#define DISPL_DC_Pin GPIO_PIN_14
#define DISPL_DC_GPIO_Port GPIOF
#define TOUCH_INT_Pin GPIO_PIN_1
#define TOUCH_INT_GPIO_Port GPIOG
#define TOUCH_INT_EXTI_IRQn EXTI1_IRQn
#define TOUCH_CS_Pin GPIO_PIN_11
#define TOUCH_CS_GPIO_Port GPIOE
#define TOUCH_SCK_Pin GPIO_PIN_10
#define TOUCH_SCK_GPIO_Port GPIOB
#define DISPL_LED_Pin GPIO_PIN_5
#define DISPL_LED_GPIO_Port GPIOB

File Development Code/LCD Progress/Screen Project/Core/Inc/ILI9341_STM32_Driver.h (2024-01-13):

#ifndef ILI9341_STM32_DRIVER_H
#define ILI9341_STM32_DRIVER_H

#include "stm32l4xx_hal.h"

extern SPI_HandleTypeDef hspi1;

#define ILI9341_SCREEN_HEIGHT 	240
#define ILI9341_SCREEN_WIDTH 	320

/* PIN Configuration */
#define HSPI_INSTANCE			&hspi1
#define LCD_CS_PORT				GPIOF
#define LCD_CS_PIN				GPIO_PIN_13
#define LCD_DC_PORT				GPIOF
#define LCD_DC_PIN				GPIO_PIN_14
#define	LCD_RST_PORT			GPIOF
#define	LCD_RST_PIN				GPIO_PIN_12

#define BURST_MAX_SIZE 			500
#define BLACK      				0x0000
#define NAVY        			0x000F
#define DARKGREEN   			0x03E0
#define DARKCYAN    			0x03EF
#define MAROON      			0x7800
#define PURPLE      			0x780F
#define OLIVE       			0x7BE0
#define LIGHTGREY   			0xC618
#define DARKGREY    			0x7BEF
#define BLUE        			0x001F
#define GREEN       			0x07E0
#define CYAN        			0x07FF
#define RED         			0xF800
#define MAGENTA     			0xF81F
#define YELLOW      			0xFFE0
#define WHITE       			0xFFFF
#define ORANGE      			0xFD20
#define GREENYELLOW 			0xAFE5
#define PINK        			0xF81F

#define SCREEN_VERTICAL_1		0
#define SCREEN_HORIZONTAL_1		1
#define SCREEN_VERTICAL_2		2
#define SCREEN_HORIZONTAL_2		3

void ILI9341_WriteCommand(uint8_t cmd);
void ILI9341_WriteData(uint8_t data);
void ILI9341_WriteBuffer(uint8_t *buffer, uint16_t len);
void ILI9341_Reset(void);
void ILI9341_Enable(void);
void ILI9341_Init(void);
void ILI9341_SetRotation(uint8_t rotation);
void ILI9341_SetAddress(uint16_t x1, uint16_t y1, uint16_t x2, uint16_t y2);
void ILI9341_DrawColor(uint16_t color);
void ILI9341_DrawColorBurst(uint16_t color, uint32_t size);
void ILI9341_FillScreen(uint16_t color);
void ILI9341_DrawPixel(uint16_t x,uint16_t y,uint16_t color);
void ILI9341_DrawRectangle(uint16_t x, uint16_t y, uint16_t width, uint16_t height, uint16_t color);
void ILI9341_DrawHLine(uint16_t x, uint16_t y, uint16_t width, uint16_t color);
void ILI9341_DrawVLine(uint16_t x, uint16_t y, uint16_t height, uint16_t color);
#endif

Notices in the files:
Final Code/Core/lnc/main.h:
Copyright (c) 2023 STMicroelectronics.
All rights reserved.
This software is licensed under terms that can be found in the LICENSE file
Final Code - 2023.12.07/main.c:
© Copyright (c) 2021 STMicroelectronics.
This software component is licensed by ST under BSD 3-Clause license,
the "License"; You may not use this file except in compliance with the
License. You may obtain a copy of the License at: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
